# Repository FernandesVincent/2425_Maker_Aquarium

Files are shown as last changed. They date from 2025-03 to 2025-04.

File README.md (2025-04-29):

<header style="
      background-color: #004080;
      color: white;
      padding: 1rem;
      text-align: center;
      height: auto;">
<div class="header-title">
<h1>Aquarium Automatisé</h1>
</div>
</header>

SOMMAIRE
- Préambule
- Objectifs du projet
- Meuble
- Filtration
- Test en gouttes
- Raspberry Pi
- PCB
- Écrans
- Code
- Câblage
- Résultat et Conclusion
- Futur du projet
<h1 style="text-align: center; text-decoration: underline; font-weight: bold;">Préambule</h1>
Aujourd'hui, lorsqu'un particulier achète son aquarium il doit pouvoir gérer un nombre important de facteurs comme la température du bac, la distribution de la nourriture mais également les différents test que peux nécessité son Aquarium (ph, NO2, CO2, etc...). C'est donc dans l'idée de soulager les personnes que cela pèse de devoir s'occuper de tout ça que l'idée du projet d'aquarium automatisé et connecté m'est venue à l'esprit.
<h1 style="text-align: center; text-decoration: underline; font-weight: bold;">Objectifs du Projet</h1>
Pour répondre à la problématique énoncée durant le préambule, j'ai dessiné les différents axes et objectifs du projet énoncés ci-dessous:
- Automatisation des changements d'eau
- Contrôle simple et total sur la luminosité
- Automatisation de la distribution de la nourriture
- Automatisation des test en gouttes
- Contrôle simple de la température
- Afficher le tout sur des écrans
- Bonus : Créer une Application mobile
Afin de réaliser l'ensemble de ces objectifs, j'ai du mettre en oeuvre plusieurs compétences que j'ai pu apprendre durant mon cursus à l'ENSEA telles que:
- Découpe LASER
- Conception de PCBs
- Modélisation et impression 3D
- Sertissage de câbles
- Mécanique
- Soudure
Mais également de nouvelles comme le montage vidéo et le HTML/CSS/JS pour la création d'un site. Pour expliquer chaque partie de ce projet en détail, nous allons partir du plus gros oeuvre vers le plus petit. Commençons donc par parler du meuble qui doit supporter l'aquarium.
<h1 style="text-align: center; text-decoration: underline; font-weight: bold;">Meuble</h1>
Au vu de l'ensemble des objectifs du projet, il fallait un endroit où ranger notamment, l'électronique avec les PCBs et les câbles, le bloc de filtration externe, le dispositif d'analyse des test en gouttes ainsi que les bacs de changements d'eau. Pour répondre à ce besoin j'ai penser à la création d'un meuble pouvant supporter le poids de l'aquarium ainsi que tout ce qu'il y a à l'intérieur. Pour ce faire il a été décidé que la structure du meuble se ferait à l'aide de profilé aluminium 20x40mm et que les murs seront faits en MDF 3mm. Cependant quelques contraintes étaient présentes:
- le meuble doit au minimum faire la largeur (30cm) et la longueur(60cm) de l'aquarium.
- Il doit pouvoir accueillir 2 bacs ayant au minimum une capacité de 18L.
- Le bac doit être assez petit pour diminuer les coûts liés au profilé aluminium.
Prenant tout cela en compte, j'ai réalisés des premiers modèles 3D pour pouvoir estimer la taille du meuble et la quantité de profilé aluminium ainsi que de MDF nécessaire. Vous pouvez voir les modèles prototypes ci-dessous:
<table>
<tbody>
<tr>
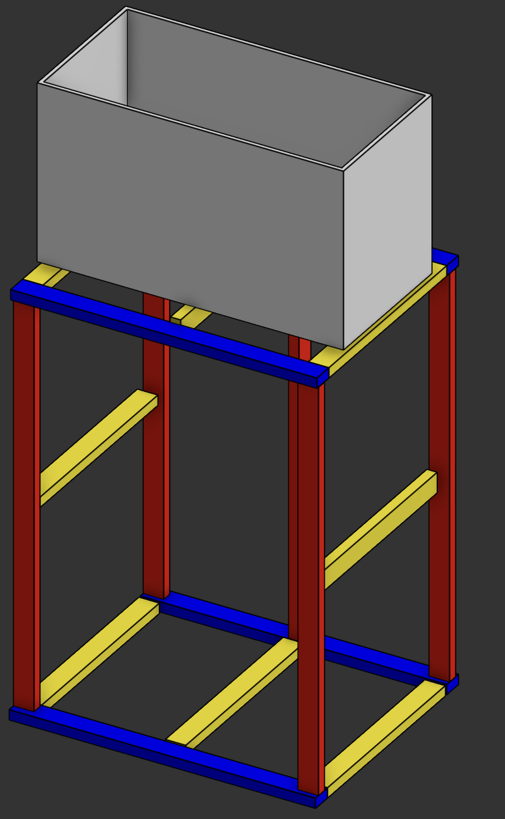
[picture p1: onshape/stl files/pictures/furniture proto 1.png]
<td></td>
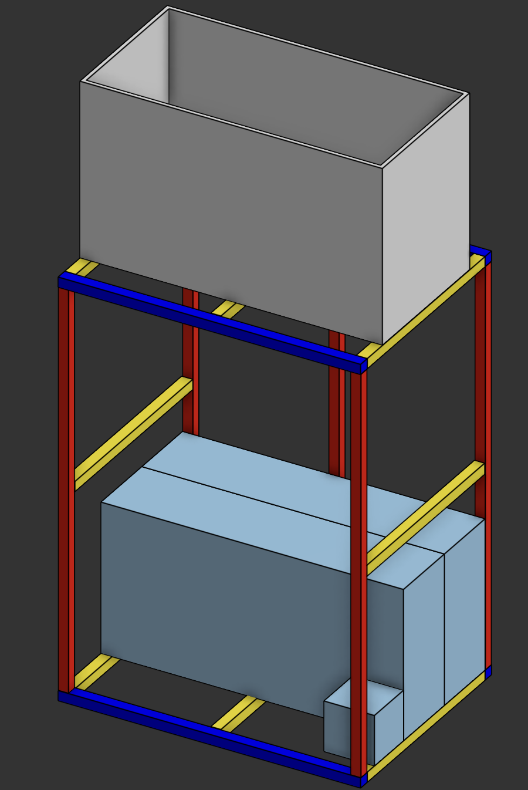
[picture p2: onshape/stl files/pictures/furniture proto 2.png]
<td></td>
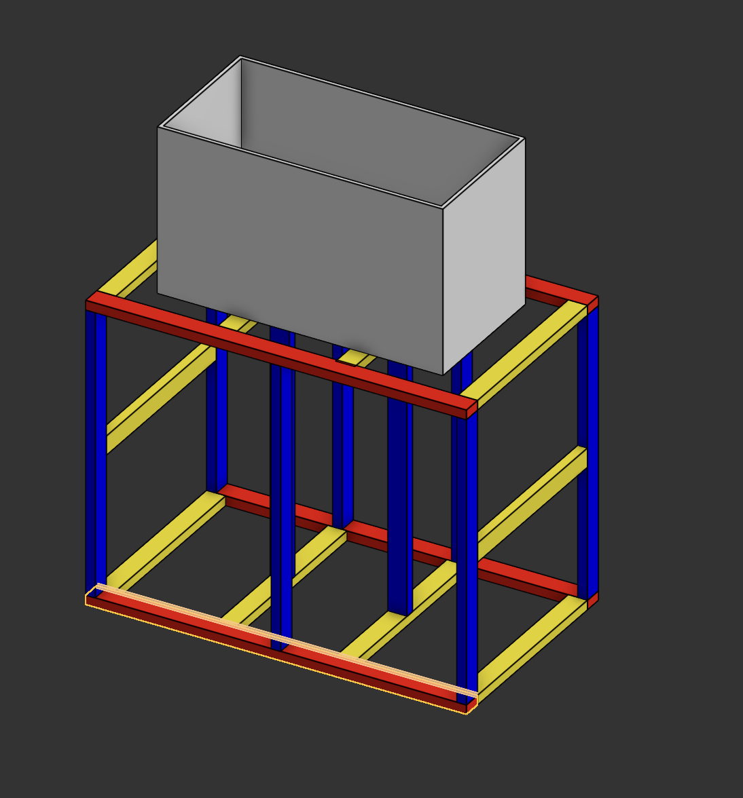
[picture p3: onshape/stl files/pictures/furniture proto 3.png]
<td></td>
</tr>
</tbody>
</table>
<table>
<tbody>
<tr>
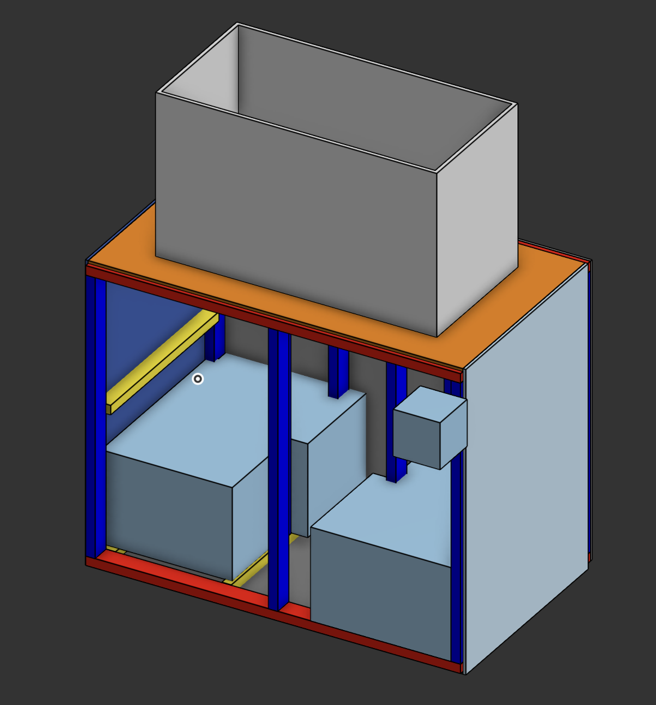
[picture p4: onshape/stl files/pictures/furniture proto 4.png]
<td></td>
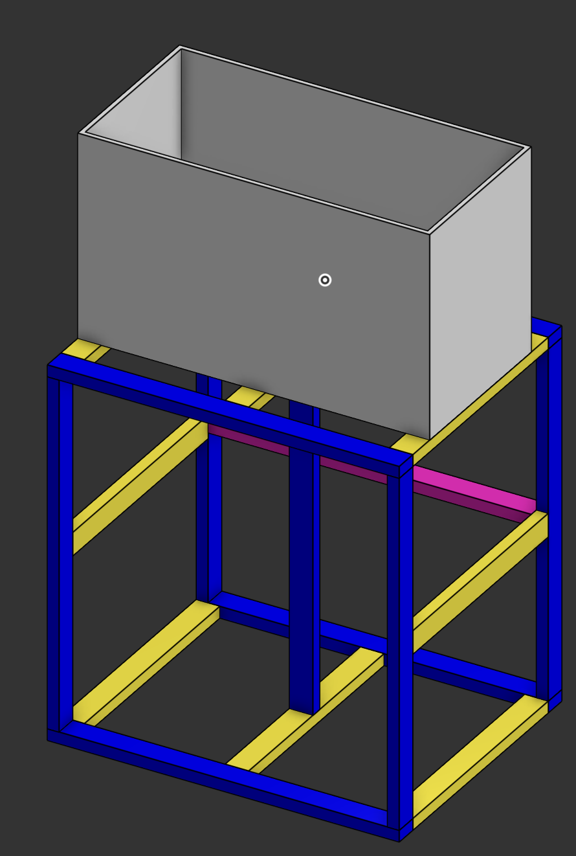
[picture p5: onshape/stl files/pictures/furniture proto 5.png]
<td></td>
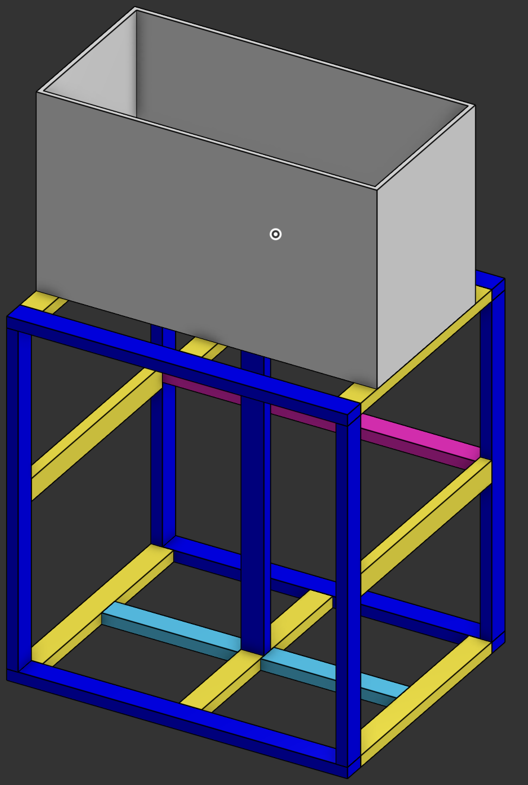
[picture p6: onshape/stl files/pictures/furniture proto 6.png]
<td></td>
</tr>
</tbody>
</table>
La version finale étant la suivante :
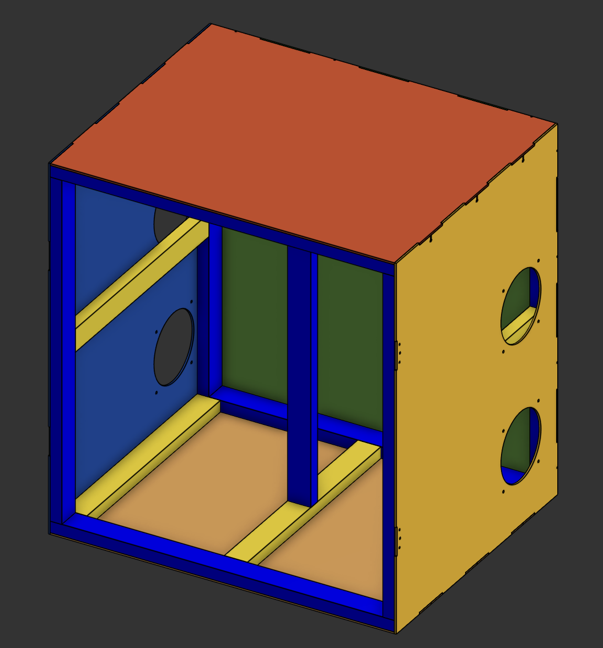
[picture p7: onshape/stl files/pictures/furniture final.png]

L'ensemble des fichiers STL est disponible sur mon
<a href="https://github.com/FernandesVincent/2425_Maker_Aquarium">GitHub</a>
dans la catégorie "onshape".
Ce meuble est donc sur 2 étages, le premier étant un étage réservé aux trois bacs de changements d'eau. Chacun ayant un objectif unique:
<br/>
<br/>
Celui ci-dessous est dédié à l'eau usée de l'aquarium qui peut être réutilisée pour par exemple arroser ses plantes.
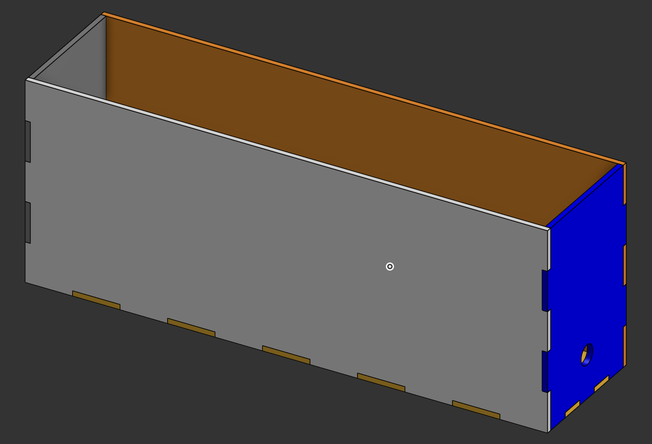
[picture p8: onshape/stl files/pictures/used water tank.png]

Le second présent ci-dessous est fait pour accueillir l'eau propre qui va venir remplacer l'eau usée.
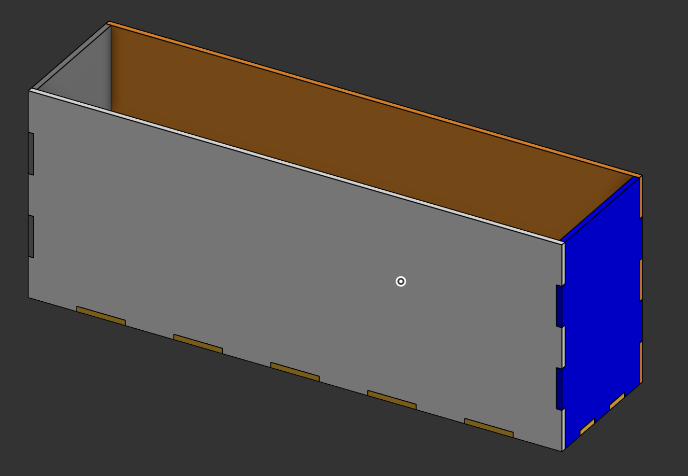
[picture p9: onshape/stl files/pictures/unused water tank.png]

Le troisième et plus petit doit est quant à lui réservé à l'eau en sortie des test à gouttes qui doit être jetée.
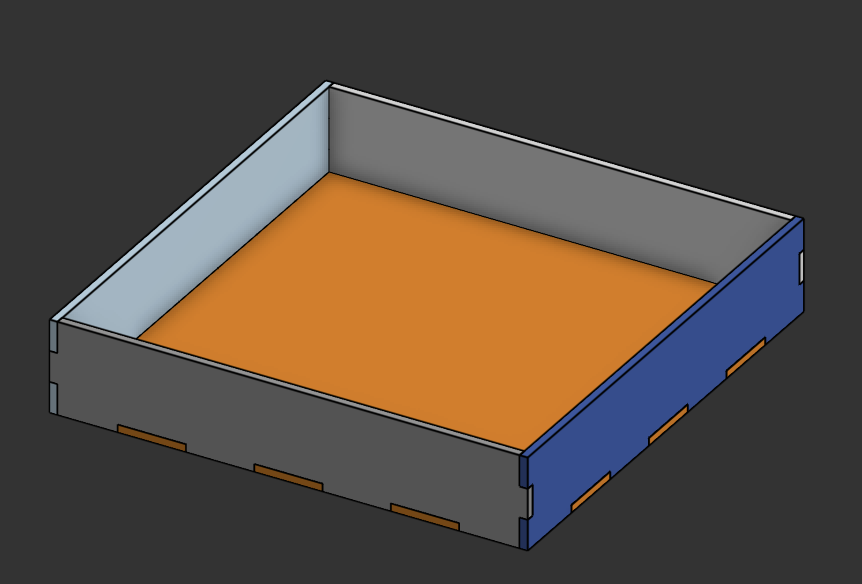
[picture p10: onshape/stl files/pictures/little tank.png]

Pour la sortie du premier bac j'ai trouver un modèle 3D de robinet qui fonctionne assez bien sur
<a href="https://www.printables.com/model/278618-water-tap">Printables</a>
.
De même que précédemment l'ensemble des fichiers STL mais également les fichiers DXF sont disponibles sur mon
<a href="https://github.com/FernandesVincent/2425_Maker_Aquarium">GitHub</a>
dans la catégorie "onshape".
<h1 style="text-align: center; text-decoration: underline; font-weight: bold;">Filtration</h1>
<br/>
Attaquons le second étage du meuble par la partie concernant le bloc de filtration. J'ai souhaité faire ce bloc externe moi-même car cela me permettait de créer un design personnalisé, notamment pour pouvoir y placer aisément le chauffage et la sonde ph en plus des masses filtrantes.
<br/>
Comme précédemment vous pouvez voir ci-dessous le prototype de ce bloc de filtration suivi de la version finale,
<br/>
<br/>
prototype:
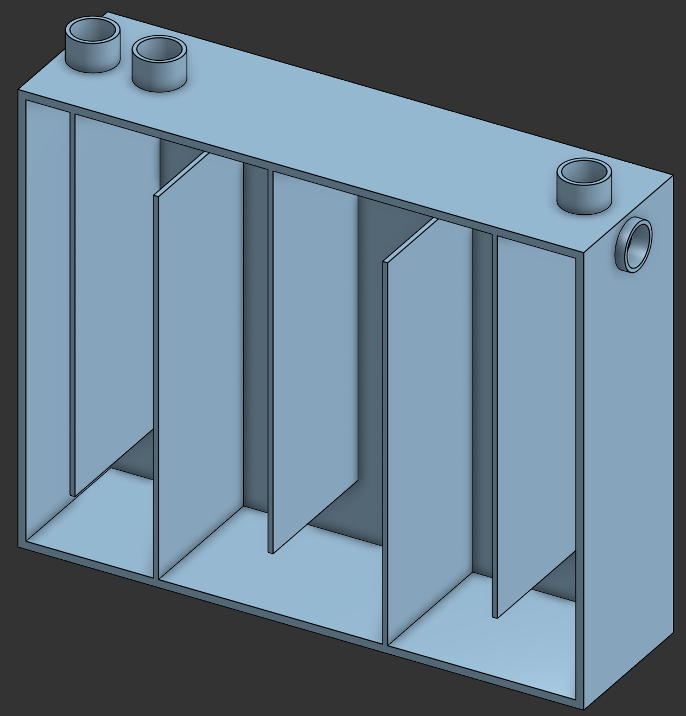
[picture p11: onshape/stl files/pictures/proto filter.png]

<br/>
version finale:
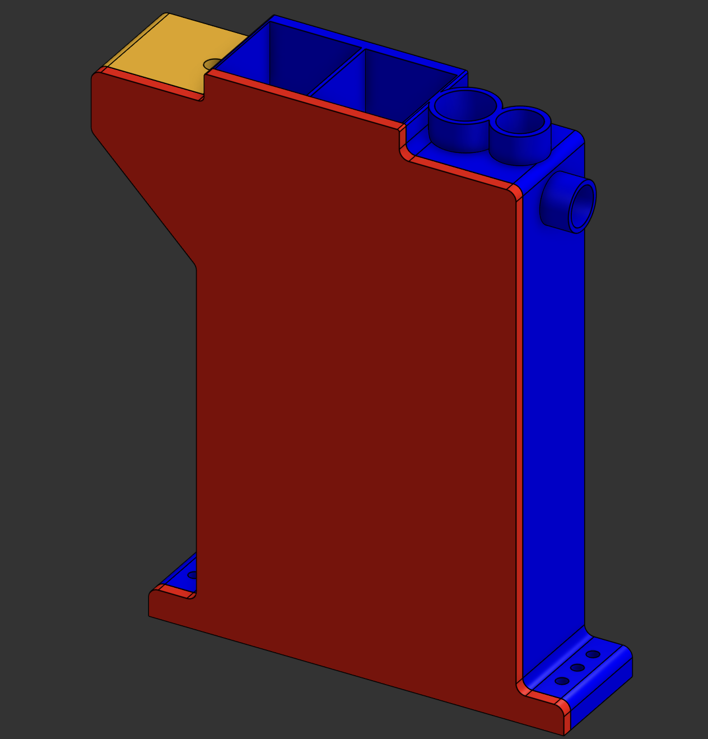
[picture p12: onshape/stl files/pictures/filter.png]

<br/>
<br/>
Pour pouvoir nettoyer les masses filtrantes, j'ai designer un bac de remonté (trouer pour que l'eau s'en écoule et ne pas trempé le meuble en les sortant) avec sa poignée :
<table>
<tbody>
<tr>
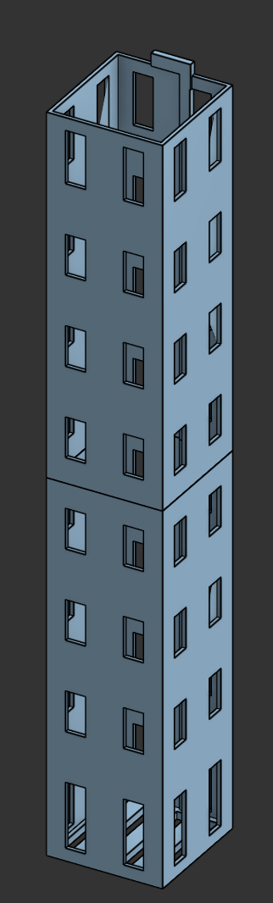
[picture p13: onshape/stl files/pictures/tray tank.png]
<td></td>
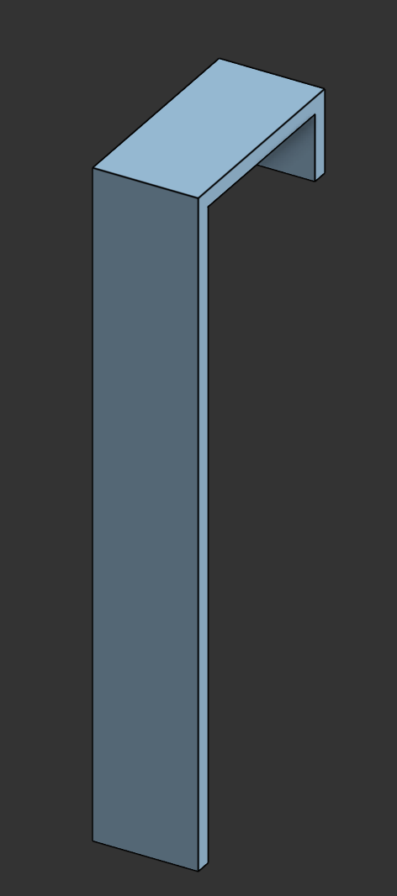
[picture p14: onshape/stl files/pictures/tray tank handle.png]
<td></td>
</tr>
</tbody>
</table>
<br/>
<br/>
Concernant les différents composants de ce bloc, la sonde ph vient de
<a href="https://wiki.dfrobot.com/Gravity__Analog_Spear_Tip_pH_Sensor___Meter_Kit__For_Soil_And_Food_Applications__SKU__SEN0249">DFRobot</a>
tandis que le chauffage est fournis avec l'aquarium qui est un aquarium de 60L de la marque CIANO disponible sur
<a href="https://www.amazon.fr/Aquarium-Poissons-Consommables-Chauffage-Emballage/dp/B0DMZ6JCDD/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">Amazon</a>
.
<br/>
De plus, concernant les masses filtrantes elles sont également disponibles sur Amazon:
<a href="https://www.amazon.fr/Fluval-Pr%C3%A9filtre-pour-Aquariophilie-750/dp/B001CZXZEU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">céramique</a>
;
<a href="https://www.amazon.fr/cyclingcolors-d%C3%A9couper-300x210mm-Universelle-%C3%A9paisseur/dp/B0B8JQTZXK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">mousse</a>
.
<br/>
Les trous dans le Blocs de filtration servent à le fixer dans le plancher à mi hauteur du meuble, ils correspondent à des vis de taille M6 avec une longueur qui doit être d'environ 20 mm sachant que le plancher est fait en MDF 6mm. Des écrous adéquat sont aussi à prévoir.
<br/>
Concernant l'impression du bloc de filtration, elle peut se faire en plus ou moins de parties en fonction de la taille de l'imprimantes. Par exemple, avec les imprimantes disponibles à l'ENSEA :
<br/>
<br/>
Creality K1 Max (300x300x300mm) : 2 parties
<br/>
BambuLab X1 Carbon(250x250x250mm) : 4 parties (les 2 parties précédentes doivent être coupées à mi-hauteur)
<br/>
<br/>
De plus, le bloc a été imprimé en PLA, or le PLA n'est pas étanche. Pour pallier à ce problème j'ai pris l'initiative d'utiliser de la résine époxy afin de vernir le bloc et de le rendre étanche. Le seul inconvénient de cette méthode est la toxicité de la résine notamment durant la phase de catalyse qui peut durer plusieurs heures et nécessite le port d'un
<a href="https://www.amazon.fr/AirGearPro-Protection-Respiratoire-R%C3%A9utilisable-poussi%C3%A8re/dp/B08BQNKK8D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">masque</a>
et de
<a href="https://www.amazon.fr/ARNOMED-jetables-pi%C3%A8ces-nitrile-disponibles/dp/B093SWH4D8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">gants de protection</a>
.
<br/>
<br/>
Pour finir, l'eau arrive du côté de la sonde PH via un tuyaux avec un OD de 20mm et elle ressort de l'autre côté grâce à une pompe de remontée connecter via un raccord à un autre tuyaux.
<br/>
<br/>
<h1 style="text-align: center; text-decoration: underline; font-weight: bold;">Test en gouttes</h1>
Au sein du meuble et à côté du bloc de filtration nous pouvons retrouver la partie test en gouttes du projet. Cette partie est surement la plus complexe du projet car elle implique la modélisation 3D d'un dispositif permettant d'insérer et d'enlever les test en gouttes mais également de pouvoir faire tomber des gouttes lorsque l'on le désire.
<br/>
<br/>
La version actuelle a été réfléchie avec un servomoteur FS90 actionnant un engrenage qui permet à son tour de faire tourner des "bras" qui iront appuyer sur les test afin de faire tomber les gouttes.
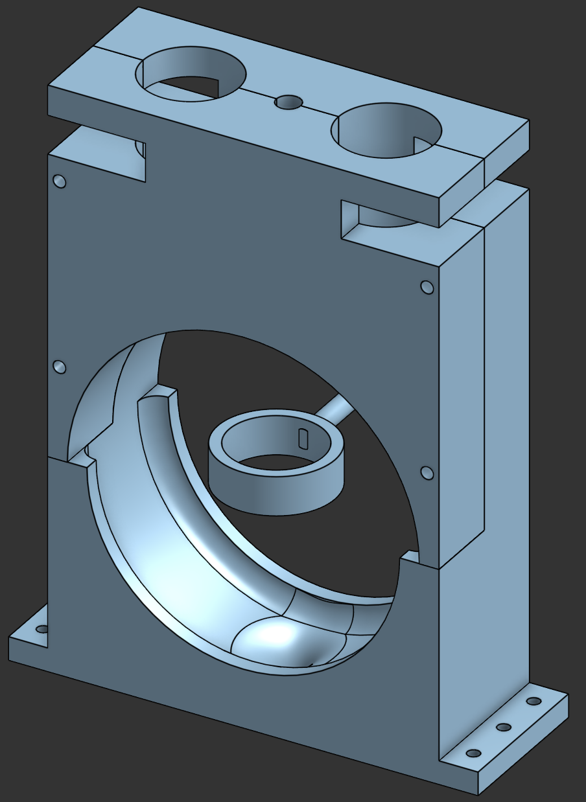
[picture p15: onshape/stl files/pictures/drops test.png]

<br/>
<br/>
Ce mécanisme est malheuresement encore en phase de prototypage car la faible tension de surface au niveau de la sortie goutte à goutte des test implique qu'une seule petite vibration peut faire s'écouler une goutte.
<br/>
Un autre modèle possible serait de faire directement tourner les tests via un servomoteur afin de faire s'écouler la goutte en profitant justement de la faible tension de surface.
<br/>
<br/>
Une fois la goutte écoulée, elle est redirigée dans un flacon, dans lequel s'écoule également l'eau du bac a testée, qui est bloqué par un anneau lié à un autre servomoteur lui permettant de pivoter afin de remuer la solution et enfin de vider le flacon dans un tuyaux menant au bac associé. Afin de déterminer la valeur associé au test (valeur de Ph, de NO3, etc...) il faut effectuer de la reconnaissance colorimétrique.
<h1 style="text-align: center; text-decoration: underline; font-weight: bold;">RaspberryPi</h1>
Pour effectuer la reconnaissance colorimétrique je me suis servi d'un raspberryPi 4 model B avec la module caméra associé. Cet ensemble auquel on ajoute un code en Python, disponible sur mon
<a href="https://github.com/FernandesVincent/2425_Maker_Aquarium">GitHub</a>
dans la catégorie "software", permet de récupérer la vision de la caméra et d'y définir un ou plusieurs points où l'on va vouloir analyser la couleur du pixel en leur centre :
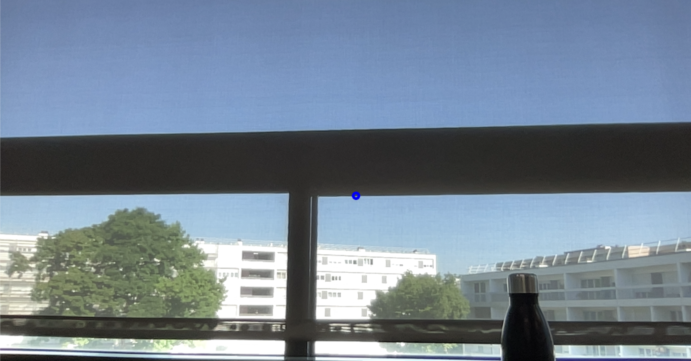
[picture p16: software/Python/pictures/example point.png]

<br/>
Le code couleur que j'ai utilisé est le HSV et non le RGB car cela permet d'être moins sensible à la différence de luminosité.
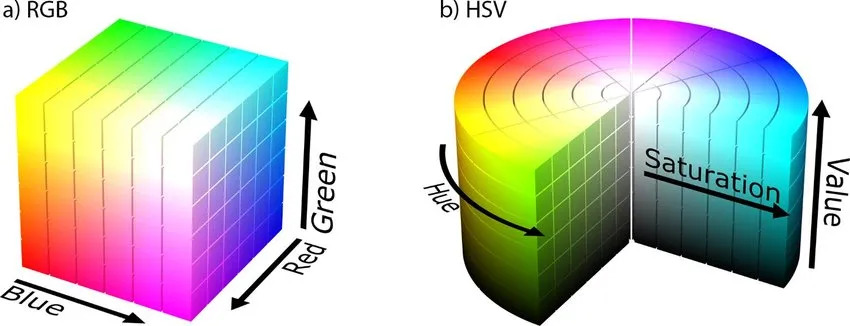
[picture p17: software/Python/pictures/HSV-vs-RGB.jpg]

<br/>
<br/>
Un aspect que je n'ai pas eu le temps de terminer est le fait de comparer les valeurs récupérés par la caméra aux valeurs de références des couleurs des test en gouttes. Cependant, l'idée derrière ce code serait d'avoir pour chaque test un tableau contenant les couleurs références et ainsi via un petit d'algorithme de comparer la couleur HSV expérimental avec celle de référence afin de l'assimiler à celle-ci.
<br/>
Finalement il suffirait de faire correspondre la couleur HSV de référence avec la valeur associée. Une fois cela fait l'objectif est de transmettre cette valeur au PCB principal qui, lui, l'enverra aux écrans.
<h1 style="text-align: center; text-decoration: underline; font-weight: bold;">PCB</h1>
Cela nous fait une transition parfaite pour parler plus en profondeur de la partie PCB du projet. En effet, pour mener à bien ce projet j'ai du réaliser 2 PCB : un premier PCB dit "principal" et un second dit "déporté". Le premier PCB et son aspect de multiprise sert à commander l'ensemble du projet, c'est à dire :
<br/>
<br/>
- Les 4 ventilateurs
- Les 4 pompes
- Les LED
- Les servomoteurs pour le distributeur de nourriture/li>
- Les boutons présents sur le second PCB
- Les écrans
- Les servomoteurs pour les test en gouttes
- la raspberryPi et sa camera
- Les capteurs de niveau d'eau
- Le Ph-mètre
- Le chauffage
- Le ST-Link
- Le HC05
Faisons un petit aparté pour détailler l'utilité de chacun des modules dont nous n'avons pas encore eu l'occasion de discuter.
<br/>
<br/>
<h4>Ventilateurs</h4>
Le meuble et le PCB sont fait pour accueillir 4
<a href="https://www.amazon.fr/ARCTIC-P12-Pack-Refroidisseur-Ventilateur/dp/B07HC7P3HJ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">ventilateurs</a>
12V de 120mmx120mm. Deux (paire entrée/sortie) à l'étage des bacs et deux ( paire entrée/sortie) à l'étage supérieur.
<br/>
Le couple de ventilateur de l'étage inférieur a pour but de ventilé l'eau propre arrivant dans le bac associé afin d'aider à l'évaporation des éléments indésirables contenu dans cette eau (si on utilise de l'eau osmosée ces deux ventilateurs sont inutiles).
<br/>
Le second couple de moteur, quant à lui, est là pour aérer la Pi, le PCB et surtout l'alimentation qui ne possède pas de ventilateur.
<h4>
<br/>
</h4>
<h4>Pompes</h4>
Pour ce projet, nous avons besoins d'un ensemble de 4
<a href="https://www.amazon.fr/submersibles-aquarium-poissons-fontaine-divertissement/dp/B0CDK7GQF2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">pompes</a>
12V 240L/h. Une première sert pour la sortie de la filtration, une seconde à remontée l'eau du bac d'eau propre à l'aquarium, une troisième à vider l'eau de l'aquarium vers le bac de récupération de l'eau usée et la dernière envoi l'eau vers le filtre. Les deux pompes liées à la filtrations fonctionnent en continu tandis que les deux autres fonctionne sur commande grâce à l'utilisation de deux transistors NMOS présents sur le PCB permettant d'allumer les pompes quand le GPIO lié à leur Ground est à l'état haut.
<h4>
<br/>
</h4>
<h4>LED</h4>
Les LED de ce projet sont séparées en deux parties mais viennent toutes de la même bande
<a href="https://www.amazon.fr/Jun-Saxifragelec-lumineuse-flexible-adressable-individuellement/dp/B0B8N4V9HW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">Neopixel</a>
.
<h4>
<br/>
</h4>
<h5>LED internes</h5>
Ce sont des LEDs coupées du ruban et placées dans le meuble afin de pouvoir l'éclairer en continu avec une même luminosité afin de limiter au mieux les erreurs de reconnaissances colorimétriques.
<h4>
<br/>
</h4>
<h5>LED externes</h5>
Ces LED sont le reste du ruban et servent directement à l'éclairage de l'aquarium. L'utilité d'avoir pris des LED Neopxiel est ici de pouvoir totalement configurer la couleur que l'on veut pour éclairer son aquarium en fonction des poissons et plantes qui l'occupe.
<h4>
<br/>
</h4>
<h4>Servomoteurs (nourriture)</h4>
Je vais traiter directement ici la partie de la distribution automatique de la nourriture car je n'ai pas eu le temps de la réaliser et par conséquent elle ne nécessite pas une partie entière à elle seule. L'objectif de cette partie était initialement de pouvoir automatiser la distribution de nourriture via un système de courroie de transmission qui amène la nourriture depuis une entrée (image ci-dessous) jusqu'à une trappe qui s'ouvre ou se ferme via l'utilisation d'un servomoteur, le tout installé à l'intérieur de la ramp LED qui éclaire l'aquarium.
<br/>
<br/>
<br/>
Ce dispositif, au même titre que les bacs de changement d'eau, permettrait à l'usager de pouvoir partir en vacances ou autre tout en sachant que les poissons seront nourris et que les changements d'eau se feront. Le problème majeur qui a fait que je n'ai pas pu réaliser cette partie est la création de la courroie de transmission qui doit être assez petite pour pouvoir faire en sorte que la rampe LED ne devienne pas trop massive autant d'un point de vu visuel que du point de vu de sa masse.
<h4>
<br/>
</h4>
<h4>Boutons</h4>
Les boutons sont placés sur le PCB secondaire et sont au nombre de 6, 3 paires de 2 boutons. Chaque paire permet d'ajuster un paramètre, la première paire permet d'ajuster la température, la deuxième la température et la troisième la fréquence de la distribution de nourriture.
<h4>
<br/>
</h4>
<h4>Écrans</h4>
Le PCB secondaire est également connecté à 6
<a href="https://www.gotronic.fr/art-afficheur-oled-0-96-128-x-64-grove-33932.htm">écrans</a>
OLED dont l'objectif est d'afficher les différents paramètres de notre système, que ce soit la température, la luminosité ou bien els différents test de l'eau.
<h4>
<br/>
</h4>
<h4>Capteurs de niveau d'eau</h4>
Ces
<a href="https://www.adafruit.com/product/4965">capteurs</a>
servent, comme leur nom l'indique, à vérifier le niveau de l'eau. Je me suis procuré ceux de Adafruit car leur prix est peu élevé et qu'ils suffisent pour l'utilité que j'en ai.
<br/>
<br/>
Lorsque deux bandes de métal entrent en contact avec de l'eau cela crée un court-circuit ce qui renvoie un signal au PCB (état haut : il ya la présence de court circuit donc l'eau à atteint le niveau que l'on veut vérifier tandis qu'à l'état bas ce n'est pas le cas). J'ai prévu d'en placer un dans l'aquarium, un autre dans le bac d'eau usée et un dernier dans le bac d'eau propre. Tout les trois servant à indiquer que l'on a atteint une hauteur limite au dessus de laquelle il se peut que l'eau se déserve des bacs.
<h4>
<br/>
</h4>
<h4>Ph-mètre</h4>
Ce Ph-mètre est fournis avec la sonde Ph et permet de rendre lisible la tension que sort la sonde Ph. Dans le futur du projet il me plairait de réussir à en faire un moi même.
<h4>
<br/>
</h4>
<h4>Chauffage</h4>
Fournis avec l'aquarium, l'objectif serait d'y connecter un servomoteur afin de pouvoir sélectionner la température que l'on souhaite avec le module externe où se trouve le PCB déporté ainsi que les écrans.
<h4>
<br/>
</h4>
<h4>ST-Link</h4>
Simplement présent pour pouvoir programmer le microprocesseur.
<h4>
<br/>
</h4>
<h4>HC05</h4>
J'ai prévu un connecteur pour le module HC05 même si l'utilisation de celui-ci ne se fera qu'à la toute fin du projet. L'objectif étant de connecter un pc ou un téléphone en bluetooth à ce module afin de récupérer l'ensemble des paramètres comme le font les écrans mais cette fois sur un pc ou un téléphone, l'objectif ultime étant le développement d'une appilcation.
<br/>
<br/>
<br/>
<br/>
<br/>
Revenons en aux PCBs, vous l'aurez compris mais ici nous avons 2 PCB avec des rôles bien distinct, le premier servant à contrôler l'ensemble du projet tandis que le second ne gère que les boutons et à se connecter aux écrans. Vous pouvez trouver ci-dessous deux photos par PCB suivies d'un lien, les photos correspondent aux schemtatic et routage des PCB effectués sous KiCad 9.0 et le fichier quant à lui est la Bill Of Material (BOM) contenant l'ensemble des composants nécessaires à la fabrication des PCB.
<br/>
<br/>
PCB principal:
<table>
<tbody>
<tr>
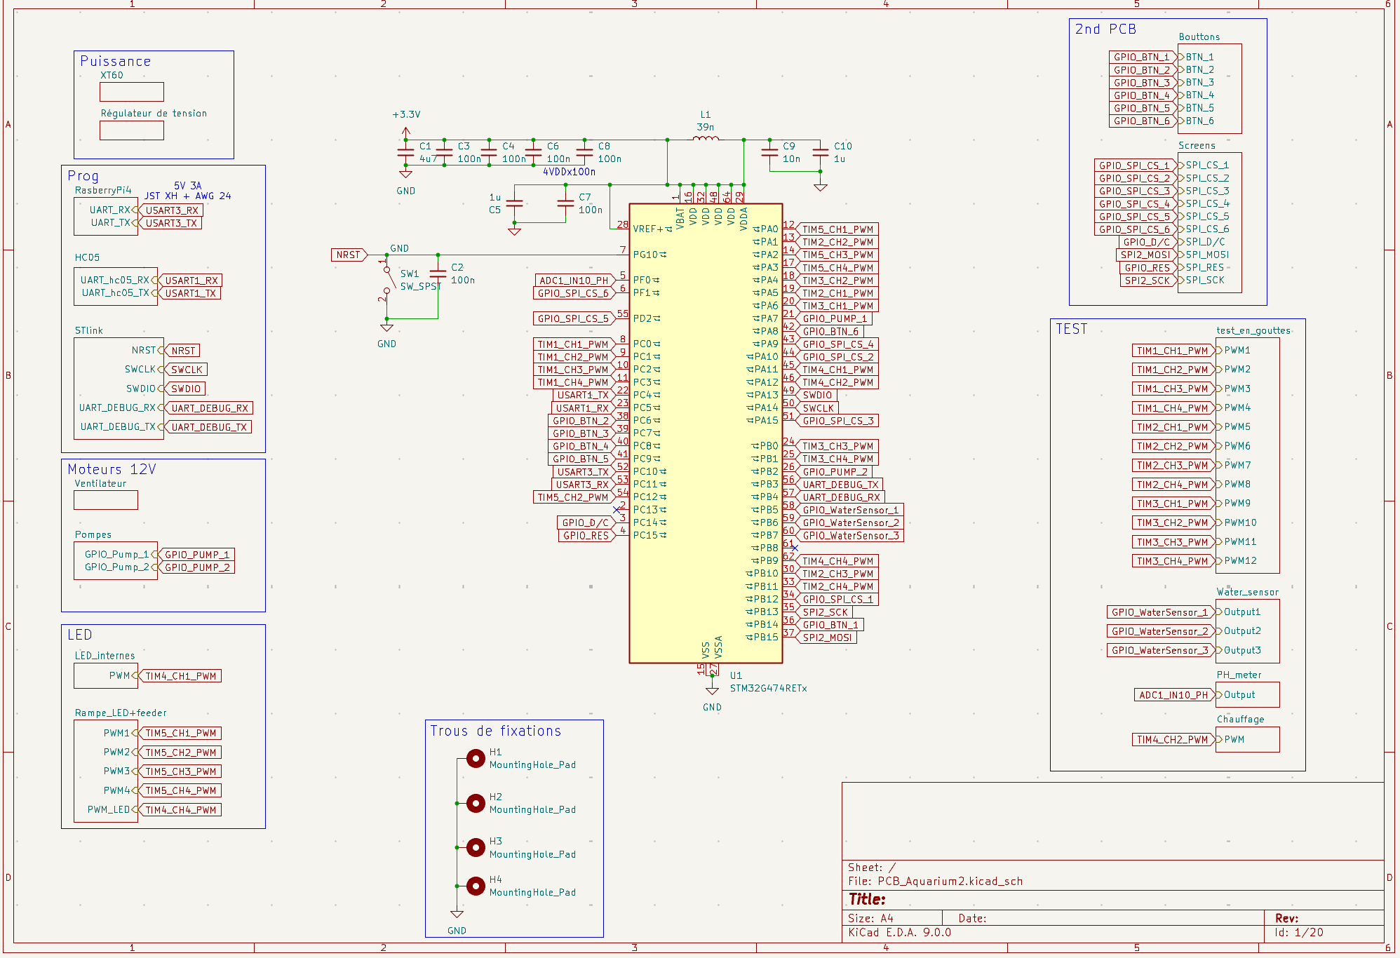
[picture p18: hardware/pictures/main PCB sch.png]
<td></td>
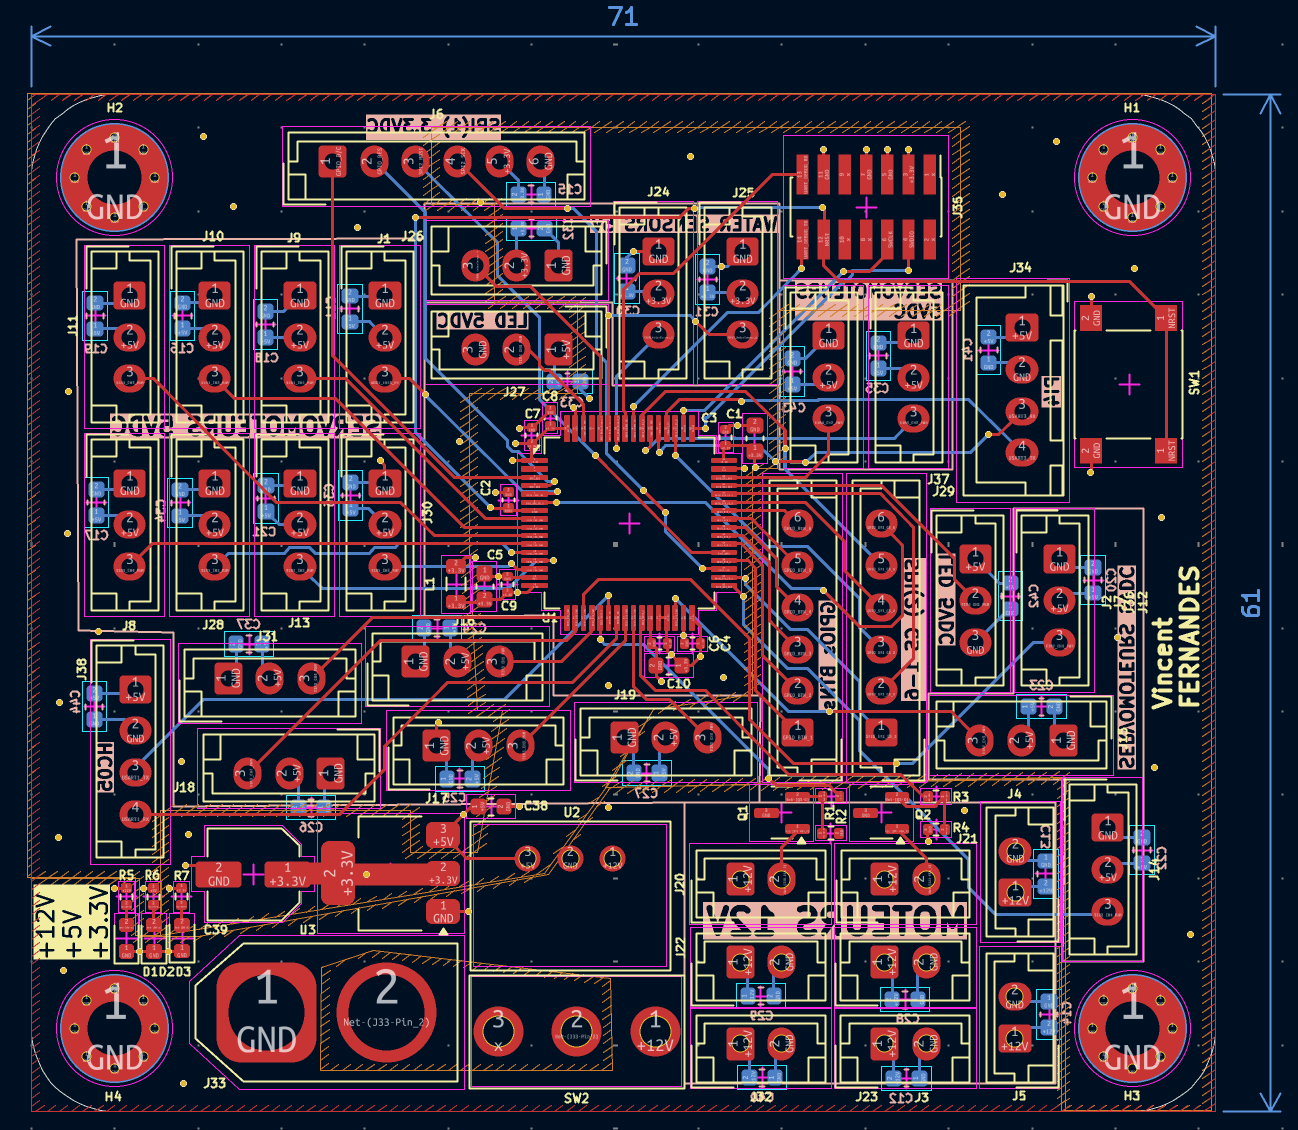
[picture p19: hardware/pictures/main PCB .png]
<td></td>
</tr>
</tbody>
</table>
<a href="https://github.com/FernandesVincent/2425_Maker_Aquarium/blob/main/hardware/PCB_Aquarium2/BOM_PDF.pdf">BOM</a>
<br/>
<br/>
PCB secondaire:
<table>
<tbody>
<tr>
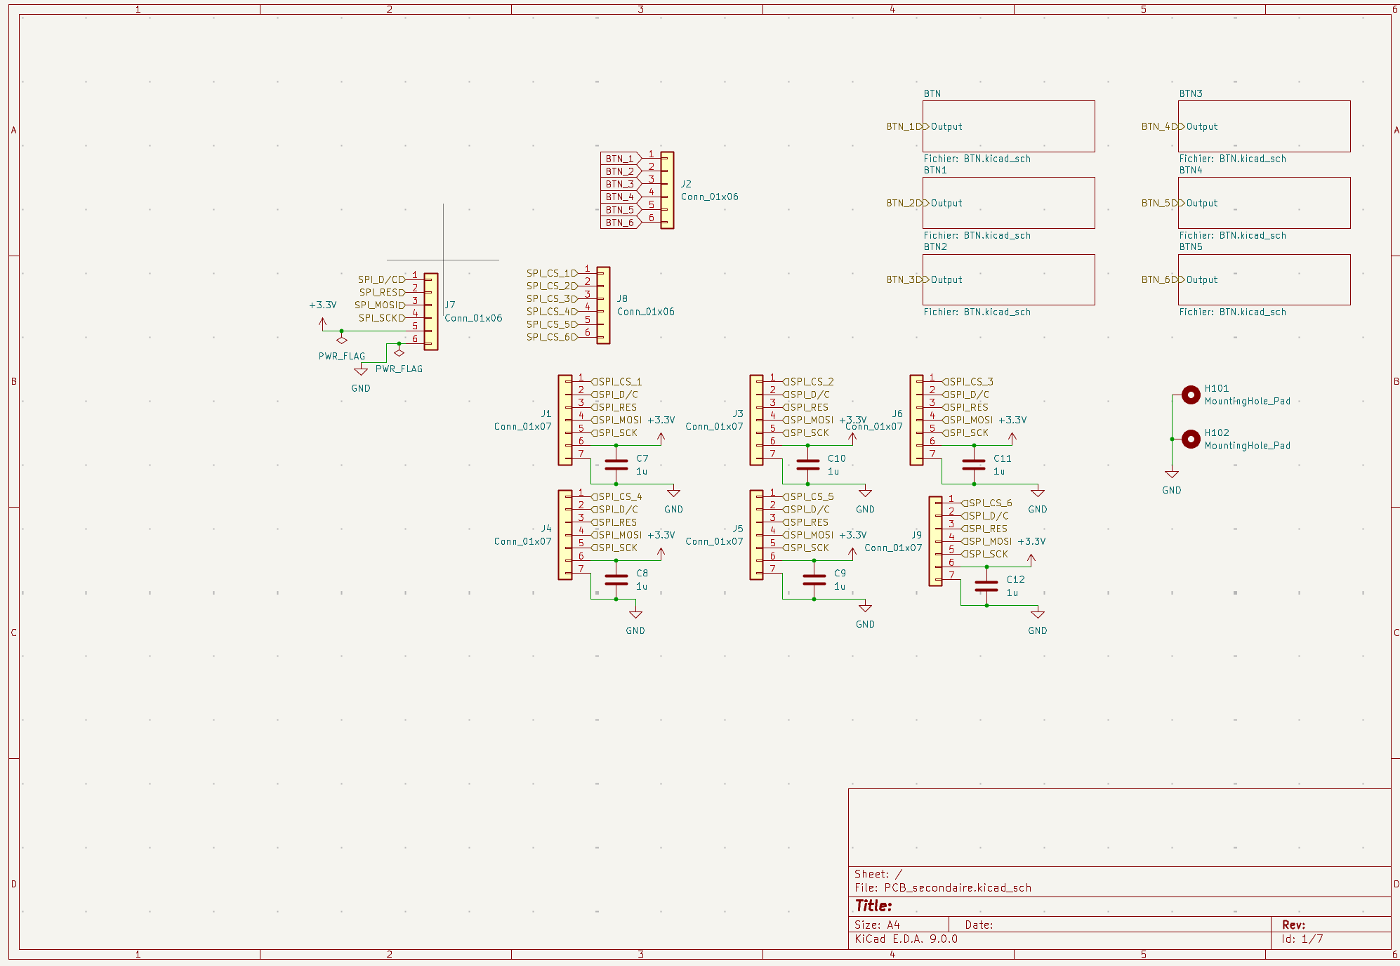
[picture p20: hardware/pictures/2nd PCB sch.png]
<td></td>
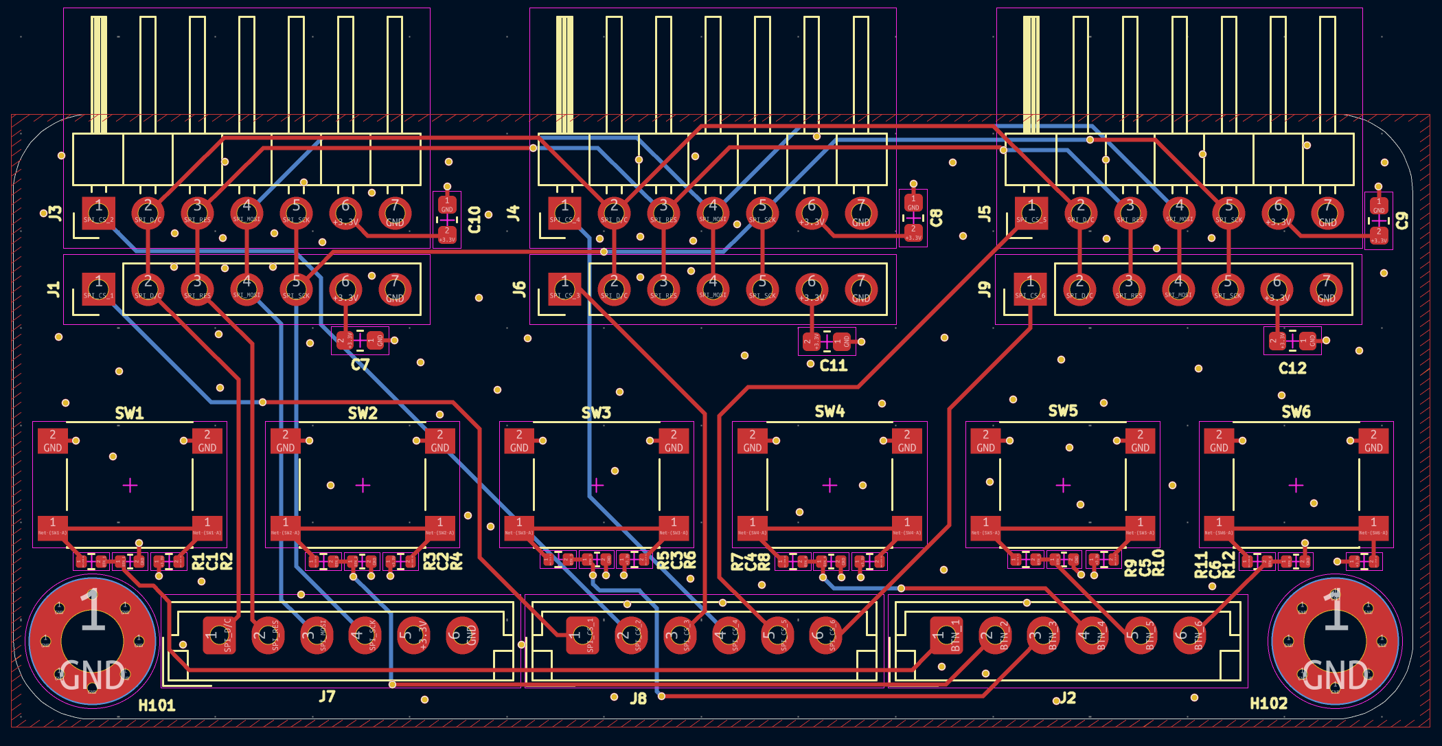
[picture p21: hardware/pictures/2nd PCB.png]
<td></td>
</tr>
</tbody>
</table>
<a href="https://github.com/FernandesVincent/2425_Maker_Aquarium/blob/main/hardware/PCB_secondaire/BOM_PDF.pdf">BOM</a>
<h1 style="text-align: center; text-decoration: underline; font-weight: bold;">Écrans</h1>
Nous avons d'ores et déjà parlé succinctement du rôle des écrans dans le projet c'est pourquoi j'aimerais m'attarder ici plutôt sur la partie code associé à ces écrans. En effet, Les écrans que j'ai commandé sont les suivants:
<br/>
<br/>
Ces écrans peuvent communiquer soit en I2C (avec 2 adresses possibles : 0x7A et 0x78) soit en SPI. Or, et je pense que vous l'avez compris avec la partie précédente mais nous avons beaucoup de modules différents avec lesquels le microprocesseur doit communiquer. Le microprocesseur en question est le STM32G474RET6 qui possède 3 I2C, ce qui est parfait pour notre projet car nous pouvons commander 2 écrans avec un seul I2C. Mais à cause du nombre très élevés du nombre de pins que le microprocesseur doit allouer au reste du projet, les pins que les 3 I2C utilisent ne sont plus disponibles.
<br/>
Il m'a donc fallu me rabattre sur le SPI qui bien que nécessitant un nombre de pins plus élevés est plus pratique dans ce cas pour deux : 1 seul SPI peut gérer les 6 écrans à conditionner de leur réservé un pin de sélection (Chip Select (CS)) chacun mais également car la plupart des pins qu'il utilise peuvent être de simple GPIO (comme CS) voir même non obligatoire en fonction de l'utilisation.
<br/>
Par exemple dans notre cas nous n'avons pas besoin du pin MOSI (Master Out Slave In) car on attend pas de réponse de la part des écrans.
<br/>
Le problème majeur que j'avais concernant le SPI est que je n'avais jamais travaillé ce protocole auparavant, j'ai donc du apprendre comment il fonctionne ce qui ne fut, heureusement, pas la partie la plus compliquée. Cependant, là où je me suis heurté à un mur c'est au moment de la recherche de librairies pour utiliser ce protocole avec le driver de mes écrans (le SSD1315) qui n'est malheureusement pas le driver le plus utilisé ce qui implique donc que les librairies que j'ai trouvées n'avaient pas directement de librairies pour ce driver, même si il semblerait que celles du driver SSD1306 fonctionne, du moins en partie, avec le SSD1315. De plus, j'ai également reçu de la part de mon encadrant une library faîte pour mon driver mais en I2C.
<br/>
Au vu du temps qu'il me restait à ce moment là j'ai préféré me concentrer sur d'autres aspects du projet ce qui fait qu'à l'heure où j'écris ces lignes, les écrans ne sont pas encore fonctionnels.
<h1 style="text-align: center; text-decoration: underline; font-weight: bold;">Code</h1>
Nous avons déjà eu l'occasion d'aborder le sujet du code dans ce projet mais j'aimerais y dédier une partie car il y a quand même des notions à ajouter et que je ne pourrais diluées dans aucune aitre partie. Veuillez tout d'abord regarder le diagramme d'architecture du code présent ci-dessous:
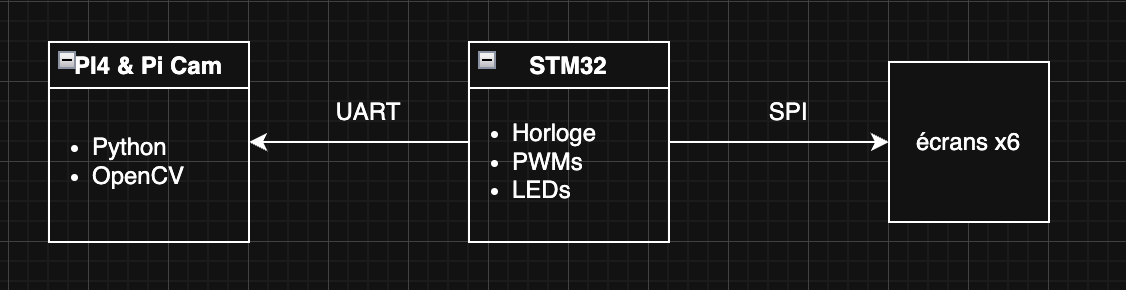
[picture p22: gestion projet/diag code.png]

<br/>
Nous avons déjà aborder la partie de la RaspberryPi excepté le fait que pour effectué la reconnaissance colorimétrique j'ai du utiliser OpenCV.
<br/>
<br/>
Concernant le code du STM32 il est, je pense, nécessaire de recontextualiser: Pour ce projet nous devons effectué des changements d'eau à un intervalle fixe (10% de l'eau de l'aquarium chaque semaine), de même il faut nourrir les poissons et effectuer les test en gouttes à intervalles réguliers. Pour effectuer cela sachant que le projet n'est pas connecté à Internet, il m'a fallu créer un horloge interne qui peux fonctionner d'elle même après avoir flasher le microprocesseur avec le code présent sur mon PC. Le fichier la contenant peut être trouver sur mon GitHub. Cette Horloge démarre à partir d'un date définit arbitrairement et permet de réaliser des actions du type : si on est au jour X à l'heure Y et à la minute Z : fait telle action.
<br/>
De plus, comme je ne commande en moteur que des servomoteurs basiques, il me suffit de leur envoyer des PWMs pour définir la position d'arrivé et ensuite les faire revenir à leur positions de départ une fois leur action finie. Le seul inconvénient de cela est que dois tester chaque mouvement de mes servomoteurs pour plusieurs valeurs de PWMs afin de pouvoir savoir quelle valeur de PWM serait la meilleure. Une méthode plus évoluée serait de créer une boucle for qui incrémente la valeur de la PWM à chaque itération.
<br/>
Finalement, Les LEDs sont commandées via DMA grâce à une librairie crée par l'un des professeurs de l'école. La seule chose est que je dois définir des valeurs références pour la couleur des LEDs afin que l'usager puisse par l'appui des boutons, passer d'une couleur à une autre. Une amélioration serait d'avoir 3 encodeur rotatif permettant à l'usager d'avoir la possibilité de régler la couleur de la lumière de son précision avec une précision qu'il n'a pas actuellement.
<h1 style="text-align: center; text-decoration: underline; font-weight: bold;">Câblage</h1>
Au vu du projet et du nombre de modules à connecter aux PCB vous vous doutez que le nombre de câbles à sertir est conséquent ! Et c'est effectivement le cas.
<br/>
Pour ce projet j'ai du sertir énormément de câbles pour différents types de connecteurs : JST EH, JST XH, Duponts. De plus, j'ai également du simplement dénuder des câbles afin de pouvoir les souder à d'autres notamment pour les pompes ou les câbles d'alimentation.
<br/>
Mais le câblage ne s'arrête pas à sertir un câble, il faut également les emballer. C'est à dire qu'il faut entourer les câble de gaine tressée pour les protéger mécaniquement et thermiquement mais également pour les organiser. Mais il faut également les entourer de gaine thermorétractable pour fixer la gaine tressée aux câbles au niveau des extrémités pour pas qu'elle ne bouge mais également au niveau des points de soudure pour protéger ce point notamment si il y a un autre câble souder à côté, ils sont ainsi isolés l'un de l'autre et l'on ne risque pas de mauvais contacts.
<h1 style="text-align: center; text-decoration: underline; font-weight: bold;">Résultat Final et Conclusion</h1>
Tout au long de cette présentation vous avez pu voir différentes parties du projet mais il est temps de montrer le résultat que j'ai réussi à obtenir à la fin de ce proje ainsi que la vidéo de présentation du projett:
<br/>
<a href="https://github.com/FernandesVincent/2425_Maker_Aquarium/blob/main/gestion%20projet/final%20result.mp4">
<br/>Résultat final</a>
<br/>
<a href="https://github.com/FernandesVincent/2425_Maker_Aquarium/blob/main/gestion%20projet/Vid%C3%A9o%20Aquarium.mp4">vidéo de présentation</a>
<br/>
<br/>
Comme vous pouvez le voir je n'ai pas pris de vidéos avec l'aquarium remplit et le système en fonctionnement et la raison à cela est simple: je n'ai pas réussi à finir et emboiter toutes les parties du projet dans le temps impartit.
<br/>
<br/>
Pour conclure cette présentation j'aimerais revenir sur ce qu'à pu m'apporter ce projet. En effet, ce projet malgré le fait que je n'ai pas pu le finir m'a quand même permis de développer toutes les compétences que l'on a pu développées au cours de cette présentation, des compétences que j'avais déjà mais que j'ai pu grandement améliorées comme la création et la soudure de PCB ou bien des compétences que je n'avais pas encore eu l'occasion de développer durant mon parcours comme la découpe LASER, la modélisation et l'impression 3D.
<br/>
Au vu de mon niveau, ce projet était sans nul doute ambitieux, surement trop d'ailleurs au vu du temps impartit mais c'est ce qui en fait un bon projet dans le sens où j'ai pu apprendre comme je n'ai jamais appris avec n'importe quel autre projet.
<h1 style="text-align: center; text-decoration: underline; font-weight: bold;">Futur du Projet</h1>
Bien évidemment je ne compte pas m'arrêter là pour ce projet. En effet, il me reste un an pour le finir avant de finir mes études et je compte bien profiter de cette année pour finir le projet et y apporter toutes les améliorations dont j'ai pu parler au sein de cette présentation et qui sait peut-être que d'autres me viendront à l'esprit entre temps !

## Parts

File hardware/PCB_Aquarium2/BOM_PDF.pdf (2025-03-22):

### BOM

Reference | Qty | Value | Footprint | MPN
C1 | 1 | 4u7 | Capacitor_SMD:C_0603_1608Metric
C2,C3,C4,C6,C7,C8 | 6 | 100n | Capacitor_SMD:C_0402_1005Metric
C5,C10,C11,C12,C13,C14,C15,C16,C17,C18,C19,C20,C21,C22,C23,C24,C25,C26,C27,C28,C29,C30,C31,C32,C33,C34,C35,C36,C37,C40,C41,C42,C43,C44 | 34 | 1u | Capacitor_SMD:C_0603_1608Metric
C9 | 1 | 10n | Capacitor_SMD:C_0402_1005Metric
C38 | 1 | 10u | Capacitor_SMD:C_0603_1608Metric
C39 | 1 | 22u | Capacitor_SMD:C_Elec_5x5.4
D1,D2,D3 | 3 | RED_LED | LED_SMD:LED_0603_1608Metric | 150060RS55040
H1,H2,H3,H4 | 4 | MountingHole_Pad | MountingHole:MountingHole_3.2mm_M3_Pad_Via
J1,J8,J9,J10,J11,J12,J13,J14,J15,J16,J17,J18,J19,J24,J25,J26,J27,J28,J29,J30,J31,J36,J37 | 23 | Conn_01x03 | Connector_JST:JST_EH_B3B-EH-A_1x03_P2.50mm_Vertical
J2,J6,J7 | 3 | Conn_01x06 | Connector_JST:JST_EH_B6B-EH-A_1x06_P2.50mm_Vertical
J3,J4,J5,J20,J21,J22,J23,J32 | 8 | Conn_01x02 | Connector_JST:JST_EH_B2B-EH-A_1x02_P2.50mm_Vertical
J33 | 1 | Conn_01x02 | Connector_AMASS:AMASS_XT60-M_1x02_P7.20mm_Vertical
J34 | 1 | Conn_01x04 | Connector_JST:JST_XH_B4B-XH-A_1x04_P2.50mm_Vertical
J35 | 1 | Conn_ST_STDC14 | Connector_PinHeader_1.27mm:PinHeader_2x07_P1.27mm_Vertical_SMD | STLINK-V3MINIE
J38 | 1 | Conn_01x04 | Connector_JST:JST_EH_B4B-EH-A_1x04_P2.50mm_Vertical
L1 | 1 | 39n | Inductor_SMD:L_0805_2012Metric
Q1,Q2 | 2 | NMOS | Package_TO_SOT_SMD:SOT-23 | SQ2310ES
R1,R3 | 2 | 1k | Resistor_SMD:R_0402_1005Metric
R2,R4 | 2 | 10k | Resistor_SMD:R_0402_1005Metric
R5 | 1 | 5k1 | Resistor_SMD:R_0402_1005Metric
R6 | 1 | 1k6 | Resistor_SMD:R_0402_1005Metric
R7 | 1 | 820 | Resistor_SMD:R_0402_1005Metric
SW1 | 1 | SW_SPST | mylib:SW_Push_1P1T_NO_6x6mm_H9.5mm
SW2 | 1 | SW_SPDT | mylib:472123010111 | 472123010111
U1 | 1 | STM32G474RETx | Package_QFP:LQFP-64_10x10mm_P0.5mm
U2 | 1 | 173010578 | Library:173010542 | 173010578
U3 | 1 | AZ1117-3.3 | Package_TO_SOT_SMD:SOT-223-3_TabPin2 | AZ1117CH2-3.3TRG1

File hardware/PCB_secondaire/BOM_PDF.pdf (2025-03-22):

### BOM_CSV

Reference | Qty | Value | Footprint
C1,C2,C3,C4,C5,C6 | 6 | 10n | Capacitor_SMD:C_0402_1005Metric
C7,C8,C9,C10,C11,C12 | 6 | 1u | Capacitor_SMD:C_0603_1608Metric
H101,H102 | 2 | MountingHole_Pad | MountingHole:MountingHole_3.2mm_M3_Pad_Via
J1,J6,J9 | 3 | Conn_01x07 | Connector_PinHeader_2.54mm:PinHeader_1x07_P2.54mm_Vertical
J2,J7,J8 | 3 | Conn_01x06 | Connector_JST:JST_EH_B6B-EH-A_1x06_P2.50mm_Vertical
J3,J4,J5 | 3 | Conn_01x07 | Connector_PinHeader_2.54mm:PinHeader_1x07_P2.54mm_Horizontal
R1,R2,R3,R4,R5,R6,R7,R8,R9,R10,R11,R12 | 12 | 10k | Resistor_SMD:R_0402_1005Metric
SW1,SW2,SW3,SW4,SW5,SW6 | 6 | SW_SPST | mylib:SW_Push_1P1T_NO_6x6mm_H9.5mm

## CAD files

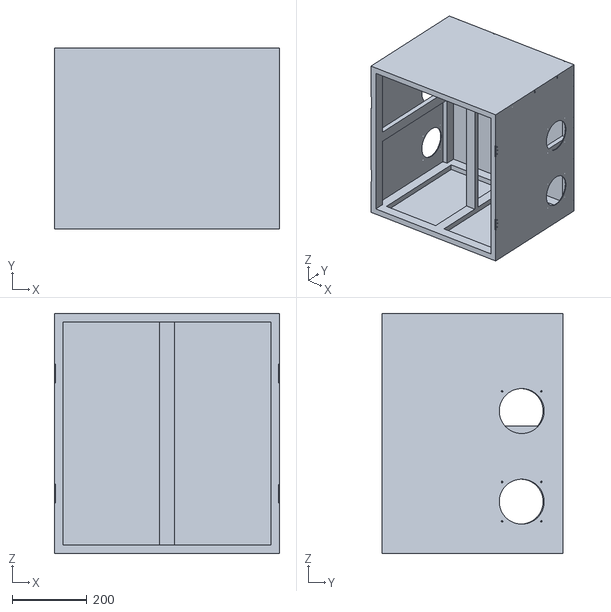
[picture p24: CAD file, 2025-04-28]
onshape/stl files/furniture assembly.stl
601.0 x 483.0 x 641.0

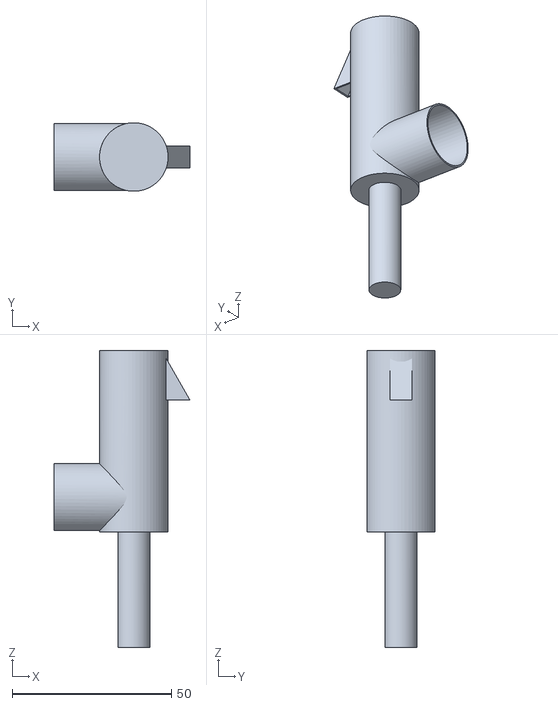
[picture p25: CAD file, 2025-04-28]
onshape/stl files/prototypes/pump assembly.stl
42.6 x 21.5 x 93.2

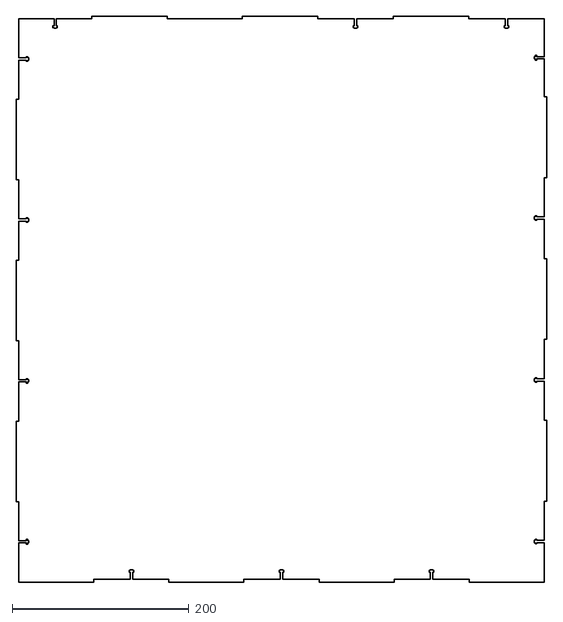
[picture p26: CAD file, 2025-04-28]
onshape/dxf files/back.dxf
601.0 x 641.0

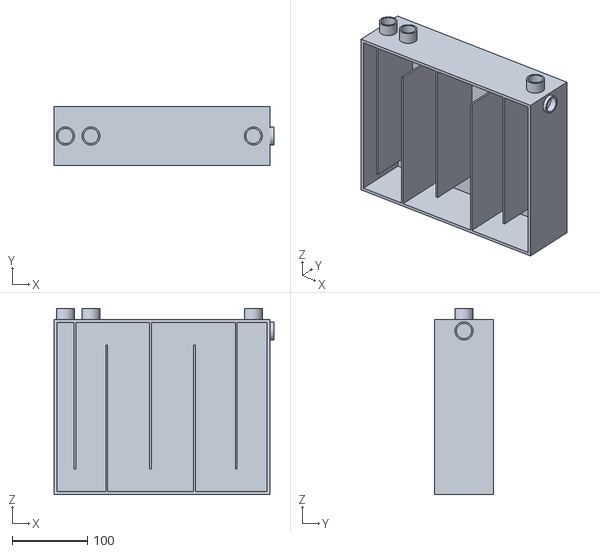
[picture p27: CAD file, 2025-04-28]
onshape/stl files/prototypes/proto filter v1.stl
293.0 x 79.0 x 248.0

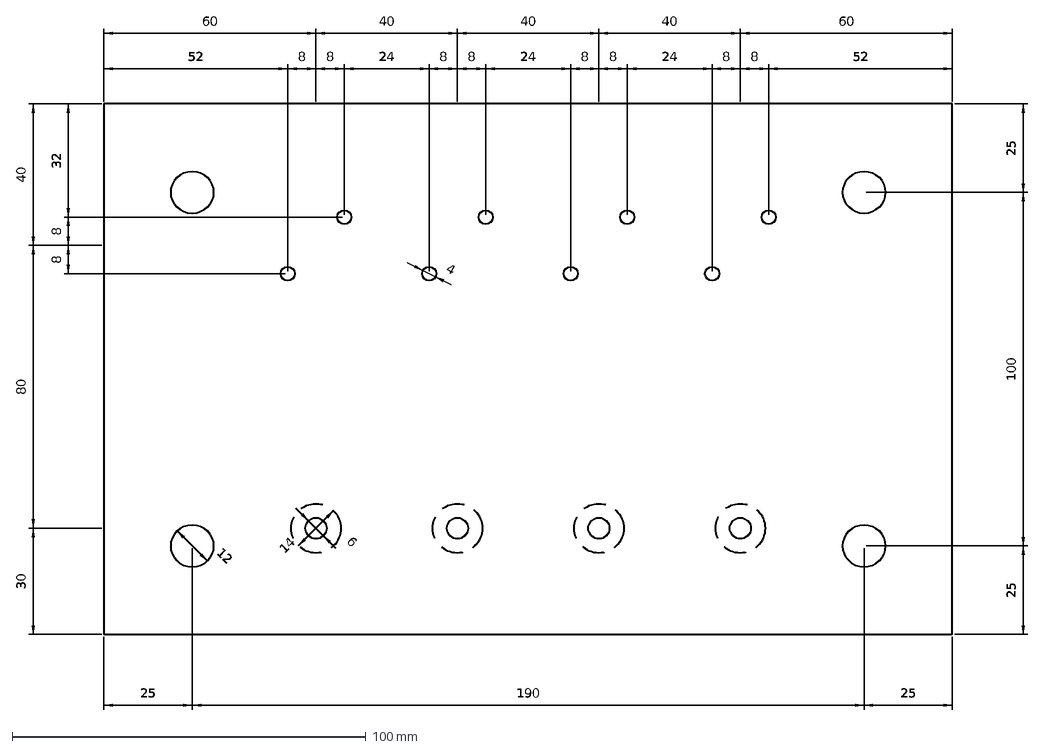
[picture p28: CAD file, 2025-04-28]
software/u8g2-master/sys/arduino/u8g2_full_buffer/SwitchBox/board.dxf
60
40
52
8
24
80
30
32
25
100
190
4
12
6
14

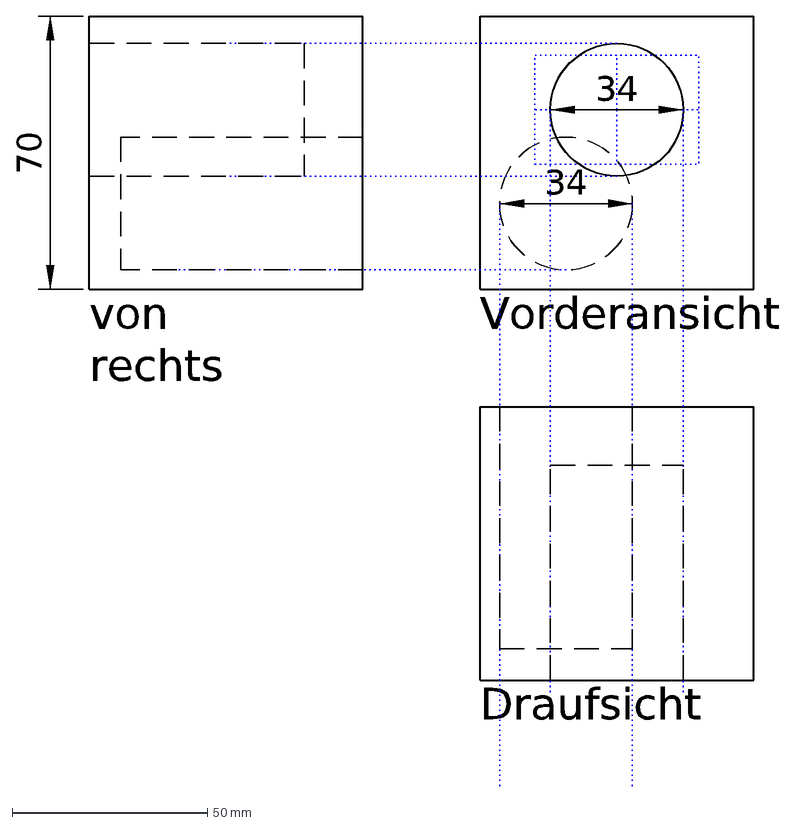
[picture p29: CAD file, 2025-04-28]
software/u8g2-master/sys/arm/stm32l031x6/clock_cube.dxf
Draufsicht
Vorderansicht
von rechts
70
34

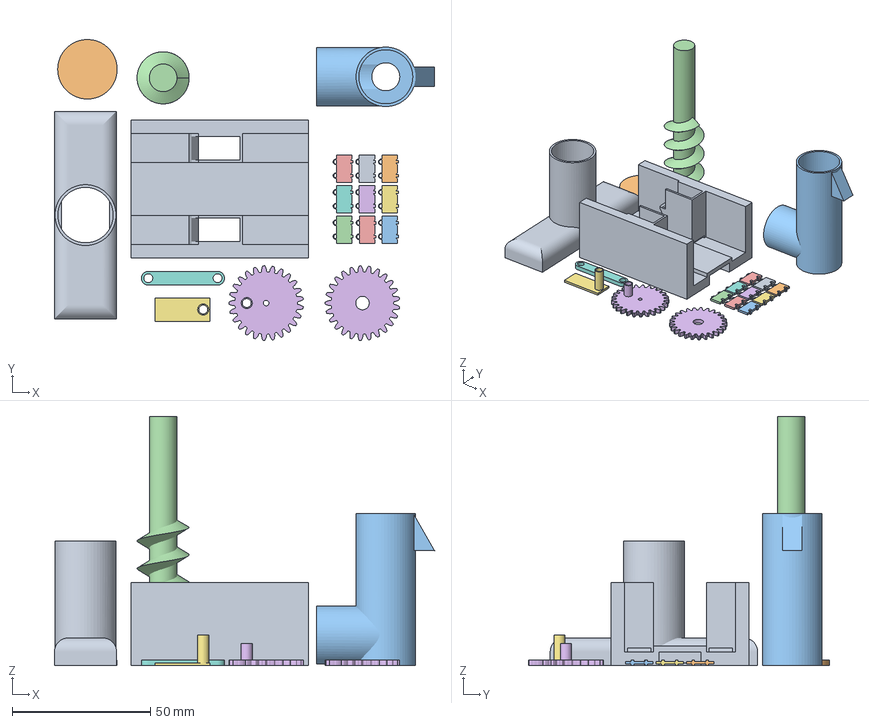
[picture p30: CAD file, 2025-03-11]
onshape/3mf files/Archi+pump.3mf
137.2 x 108.7 x 90.0 mm
pumpV2 part2.stl
visArchipart3 V2.stl
vis ArchiV2 part2.stl
visArchi V2 part1.stl
Part Studio 3 (1).stl x 9
gear V1.stl
bieleV1.stl
biele part2 V1.stl
rampe-food_cutV1.stl

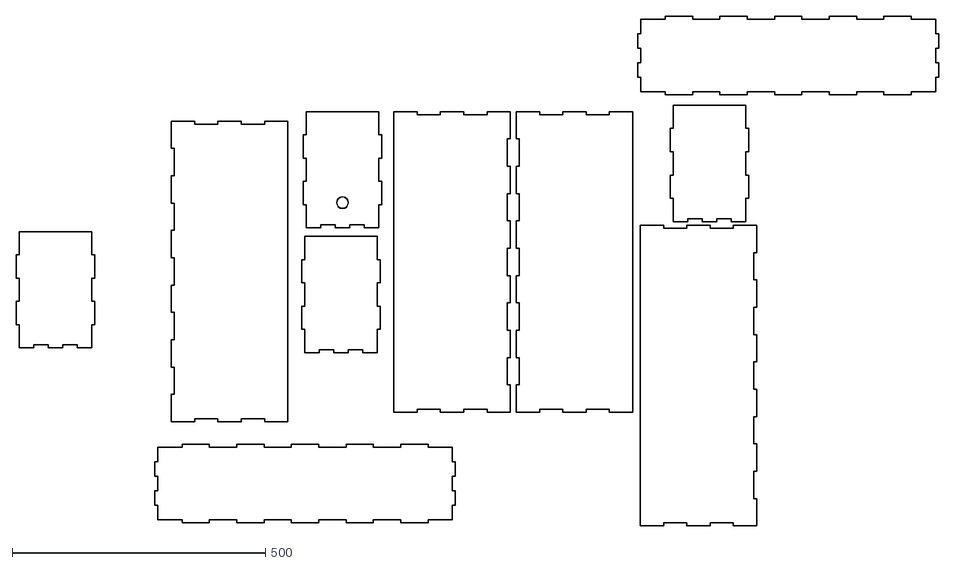
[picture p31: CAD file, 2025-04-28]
onshape/dxf files/2nd & 3rd tank.dxf
1821.6 x 1007.0

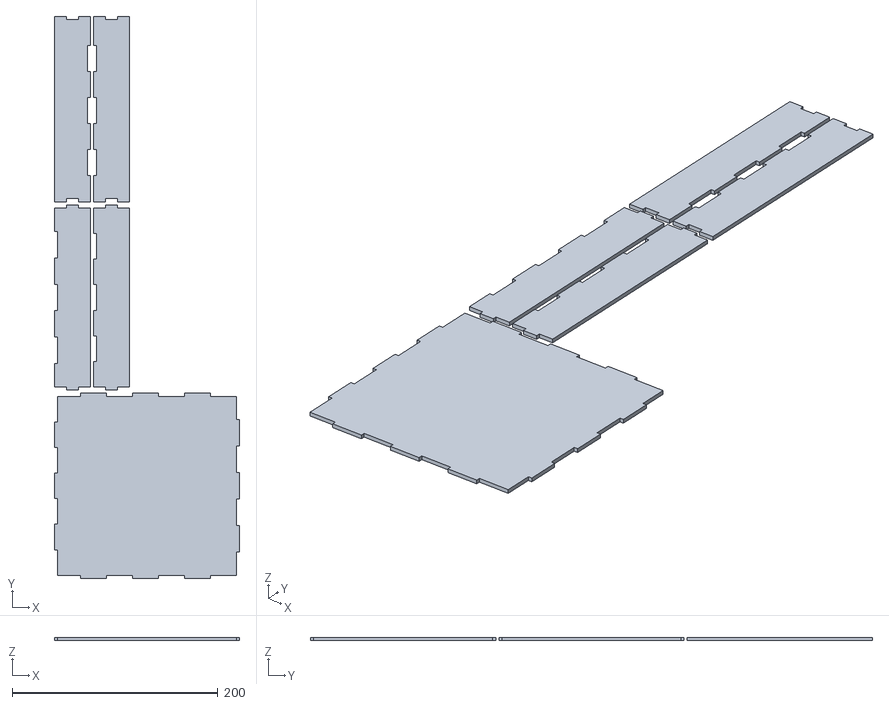
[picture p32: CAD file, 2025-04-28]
onshape/stl files/4th tank.stl
180.0 x 546.0 x 3.00

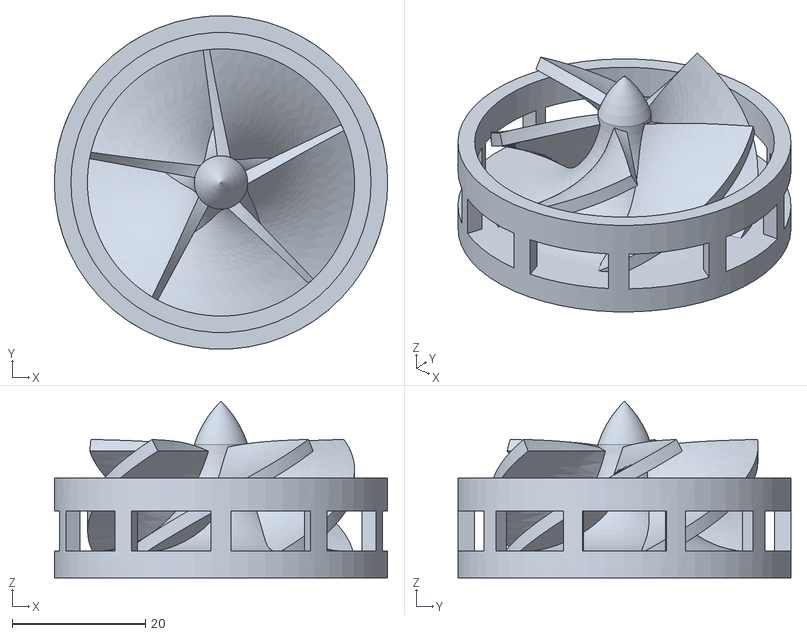
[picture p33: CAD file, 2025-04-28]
onshape/stl files/prototypes/vertical pump.stl
50.0 x 49.9 x 26.5

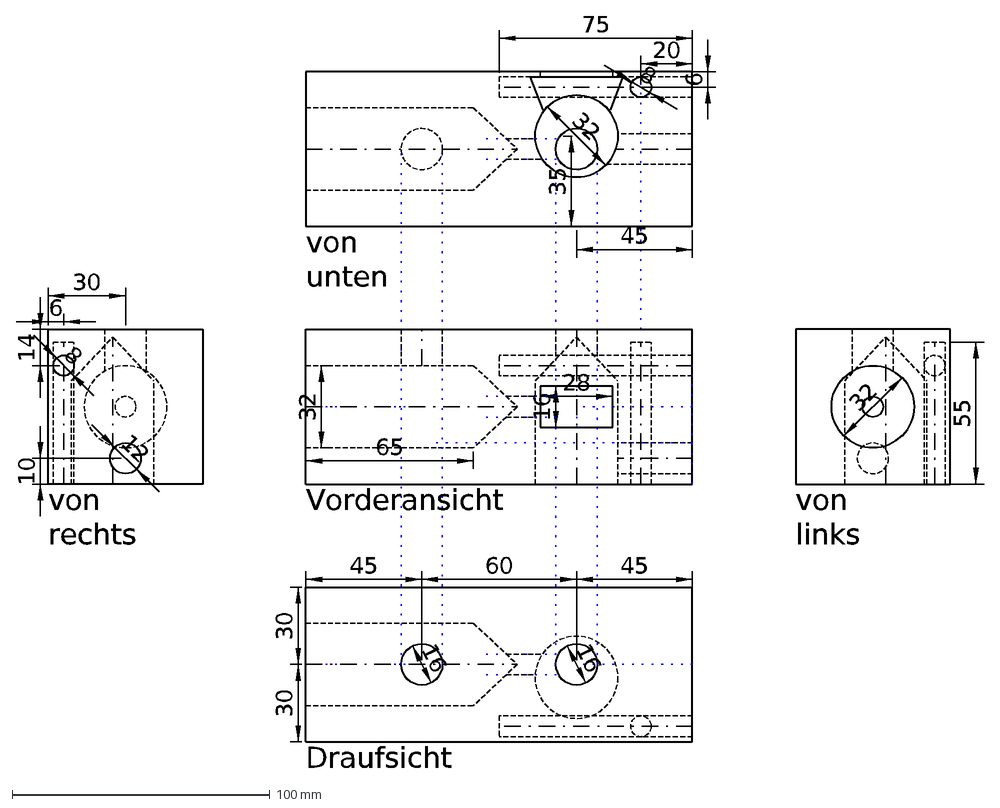
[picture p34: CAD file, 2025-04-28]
software/u8g2-master/sys/arm/stm32l031x6/clock.dxf
65
32
28
16
Draufsicht
Vorderansicht
von unten
von rechts
von links
14
6
45
60
30
20
8
35
75
55
10
12

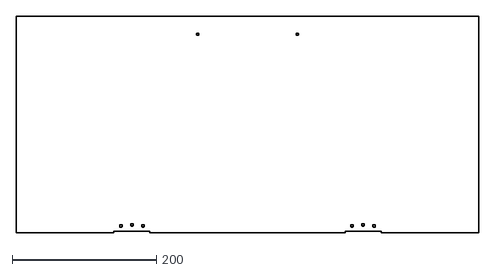
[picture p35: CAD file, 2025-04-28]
onshape/dxf files/face 2 (1).dxf
641.0 x 300.5

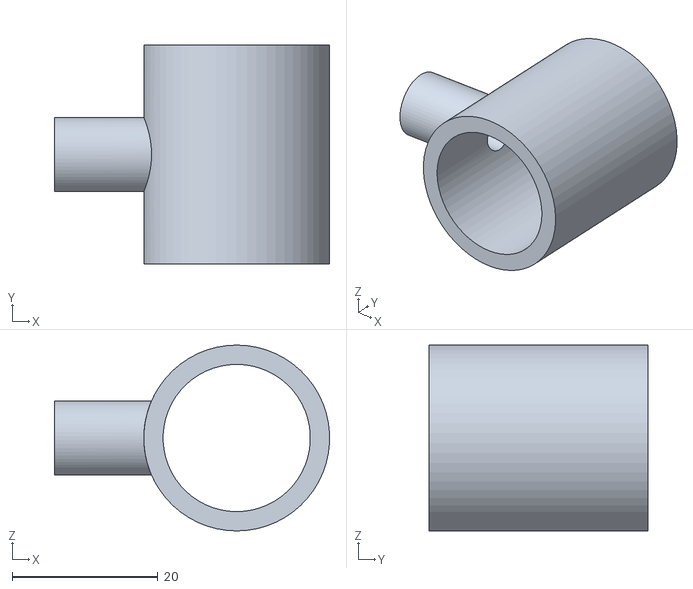
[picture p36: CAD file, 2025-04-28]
onshape/stl files/pipe connection model 2.stl
37.7 x 30.0 x 25.5

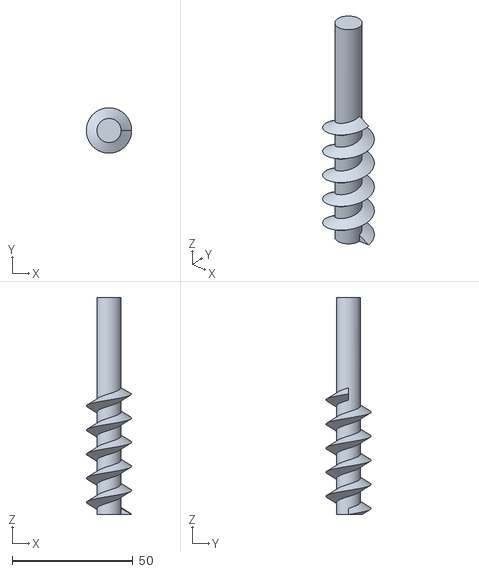
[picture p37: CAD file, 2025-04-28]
onshape/stl files/prototypes/pump part 1.stl
18.8 x 18.8 x 90.0

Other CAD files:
onshape/3mf files/filtreV3.3mf
onshape/3mf files/cacheV1.3mf
software/u8g2-master/sys/arm/stm32l031x6/clock_2.dxf
onshape/dxf files/Left & Right (1).dxf
onshape/dxf files/4th tank.dxf
onshape/dxf files/Top & Bot.dxf
onshape/dxf files/face 1.dxf
onshape/dxf files/floor.dxf
onshape/stl files/2nd tank (used water).stl
onshape/stl files/3rd tank (unused water).stl
onshape/stl files/Arms.stl
onshape/stl files/PCB protector.stl
onshape/stl files/aluminium profile.stl
onshape/stl files/drops test v2.stl
onshape/stl files/floor.stl
onshape/stl files/food entry.stl
onshape/stl files/furnitures walls.stl
onshape/stl files/gear test.stl
onshape/stl files/handle.stl
onshape/stl files/light v2.stl
onshape/stl files/motor ring.stl
onshape/stl files/pipe bloc.stl
onshape/stl files/pipe connection model 1.stl
onshape/stl files/prototypes/drops test v1.stl
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

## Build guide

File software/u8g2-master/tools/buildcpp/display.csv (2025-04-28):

# 1. device name
# 2. pinset
# 3. constructor name w/o prefix
u8x8_d_ssd1306_128x64_noname | 4WSWSPI | SSD1306_128X64_4W_SW_SPI
u8x8_d_ssd1306_128x64_noname | 4WHWSPI | SSD1306_128X64_4W_HW_SPI
u8x8_d_ssd1306_128x64_noname | 3WSWSPI | SSD1306_128X64_3W_SW_SPI
u8x8_d_ssd1306_128x64_noname | SSDSWI2C | SSD1306_128X64_SW_I2C
u8x8_d_ssd1306_128x64_noname | 6800 | SSD1306_128X64_6800
u8x8_d_ssd1306_128x64_noname | 8080 | SSD1306_128X64_8080

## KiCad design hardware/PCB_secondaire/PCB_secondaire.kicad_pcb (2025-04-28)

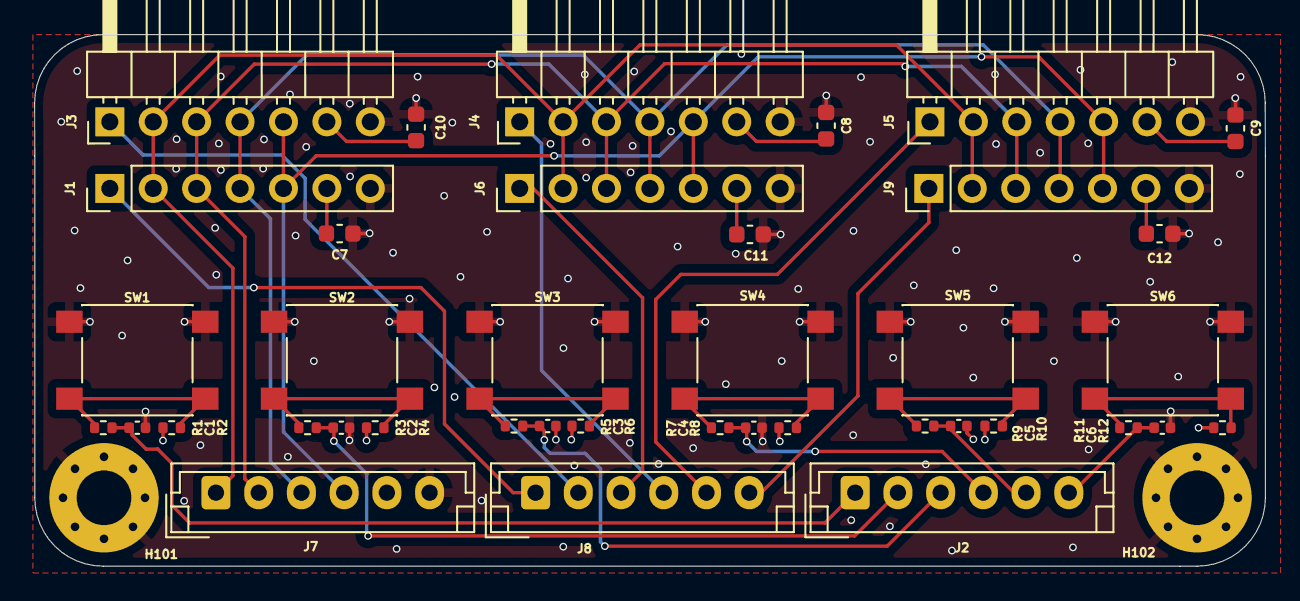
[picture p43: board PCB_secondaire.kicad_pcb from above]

Board: 4 copper layers, 72.0 x 31.1 mm, 41 parts (0 on the bottom side), 24 nets.

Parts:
C1, C2, C3, C4, C5, C6: 10n; C_0402_1005Metric
C7, C8, C9, C10, C11, C12: 1u; C_0603_1608Metric
H101, H102: MountingHole_Pad; MountingHole_3.2mm_M3_Pad_Via
J1, J6, J9: Conn_01x07; PinHeader_1x07_P2.54mm_Vertical
J2, J7, J8: Conn_01x06; JST_EH_B6B-EH-A_1x06_P2.50mm_Vertical
J3, J4, J5: Conn_01x07; PinHeader_1x07_P2.54mm_Horizontal
R1, R2, R3, R4, R5, R6, R7, R8, R9, R10, R11, R12: 10k; R_0402_1005Metric
SW1, SW2, SW3, SW4, SW5, SW6: SW_SPST; SW_Push_1P1T_NO_6x6mm_H9.5mm

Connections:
+3.3V: C7.2, C8.2, C9.2, C10.2, C11.2, C12.2, J1.6, J3.6, J4.6, J5.6, J6.6, J7.5, J9.6, R2.1, R4.1, R6.1, R8.1, R10.1, R12.1
/SPI_CS_1: J1.1, J8.1
/SPI_CS_2: J3.1, J8.2
/SPI_CS_3: J6.1, J8.3
/SPI_CS_4: J4.1, J8.4
/SPI_CS_5: J5.1, J8.5
/SPI_CS_6: J8.6, J9.1
/SPI_D/C: J1.2, J3.2, J4.2, J5.2, J6.2, J7.1, J9.2
/SPI_MOSI: J1.4, J3.4, J4.4, J5.4, J6.4, J7.3, J9.4
/SPI_RES: J1.3, J3.3, J4.3, J5.3, J6.3, J7.2, J9.3
/SPI_SCK: J1.5, J3.5, J4.5, J5.5, J6.5, J7.4, J9.5
BTN_1: C1.1, J2.1, R1.2
BTN_2: C2.1, J2.2, R3.2
BTN_3: C3.1, J2.3, R5.2
BTN_4: C4.1, J2.4, R7.2
BTN_5: C5.1, J2.5, R9.2
BTN_6: C6.1, J2.6, R11.2
GND: C1.2, C2.2, C3.2, C4.2, C5.2, C6.2, C7.1, C8.1, C9.1, C10.1, C11.1, C12.1, H101.1, H102.1, J1.7, J3.7, J4.7, J5.7, J6.7, J7.6, J9.7, SW1.2 (B), SW2.2 (B), SW3.2 (B), SW4.2 (B), SW5.2 (B), SW6.2 (B)
unnamed: R1.1, R2.2, SW1.1 (A)
unnamed: R3.1, R4.2, SW2.1 (A)
unnamed: R5.1, R6.2, SW3.1 (A)
unnamed: R7.1, R8.2, SW4.1 (A)
unnamed: R9.1, R10.2, SW5.1 (A)
unnamed: R11.1, R12.2, SW6.1 (A)

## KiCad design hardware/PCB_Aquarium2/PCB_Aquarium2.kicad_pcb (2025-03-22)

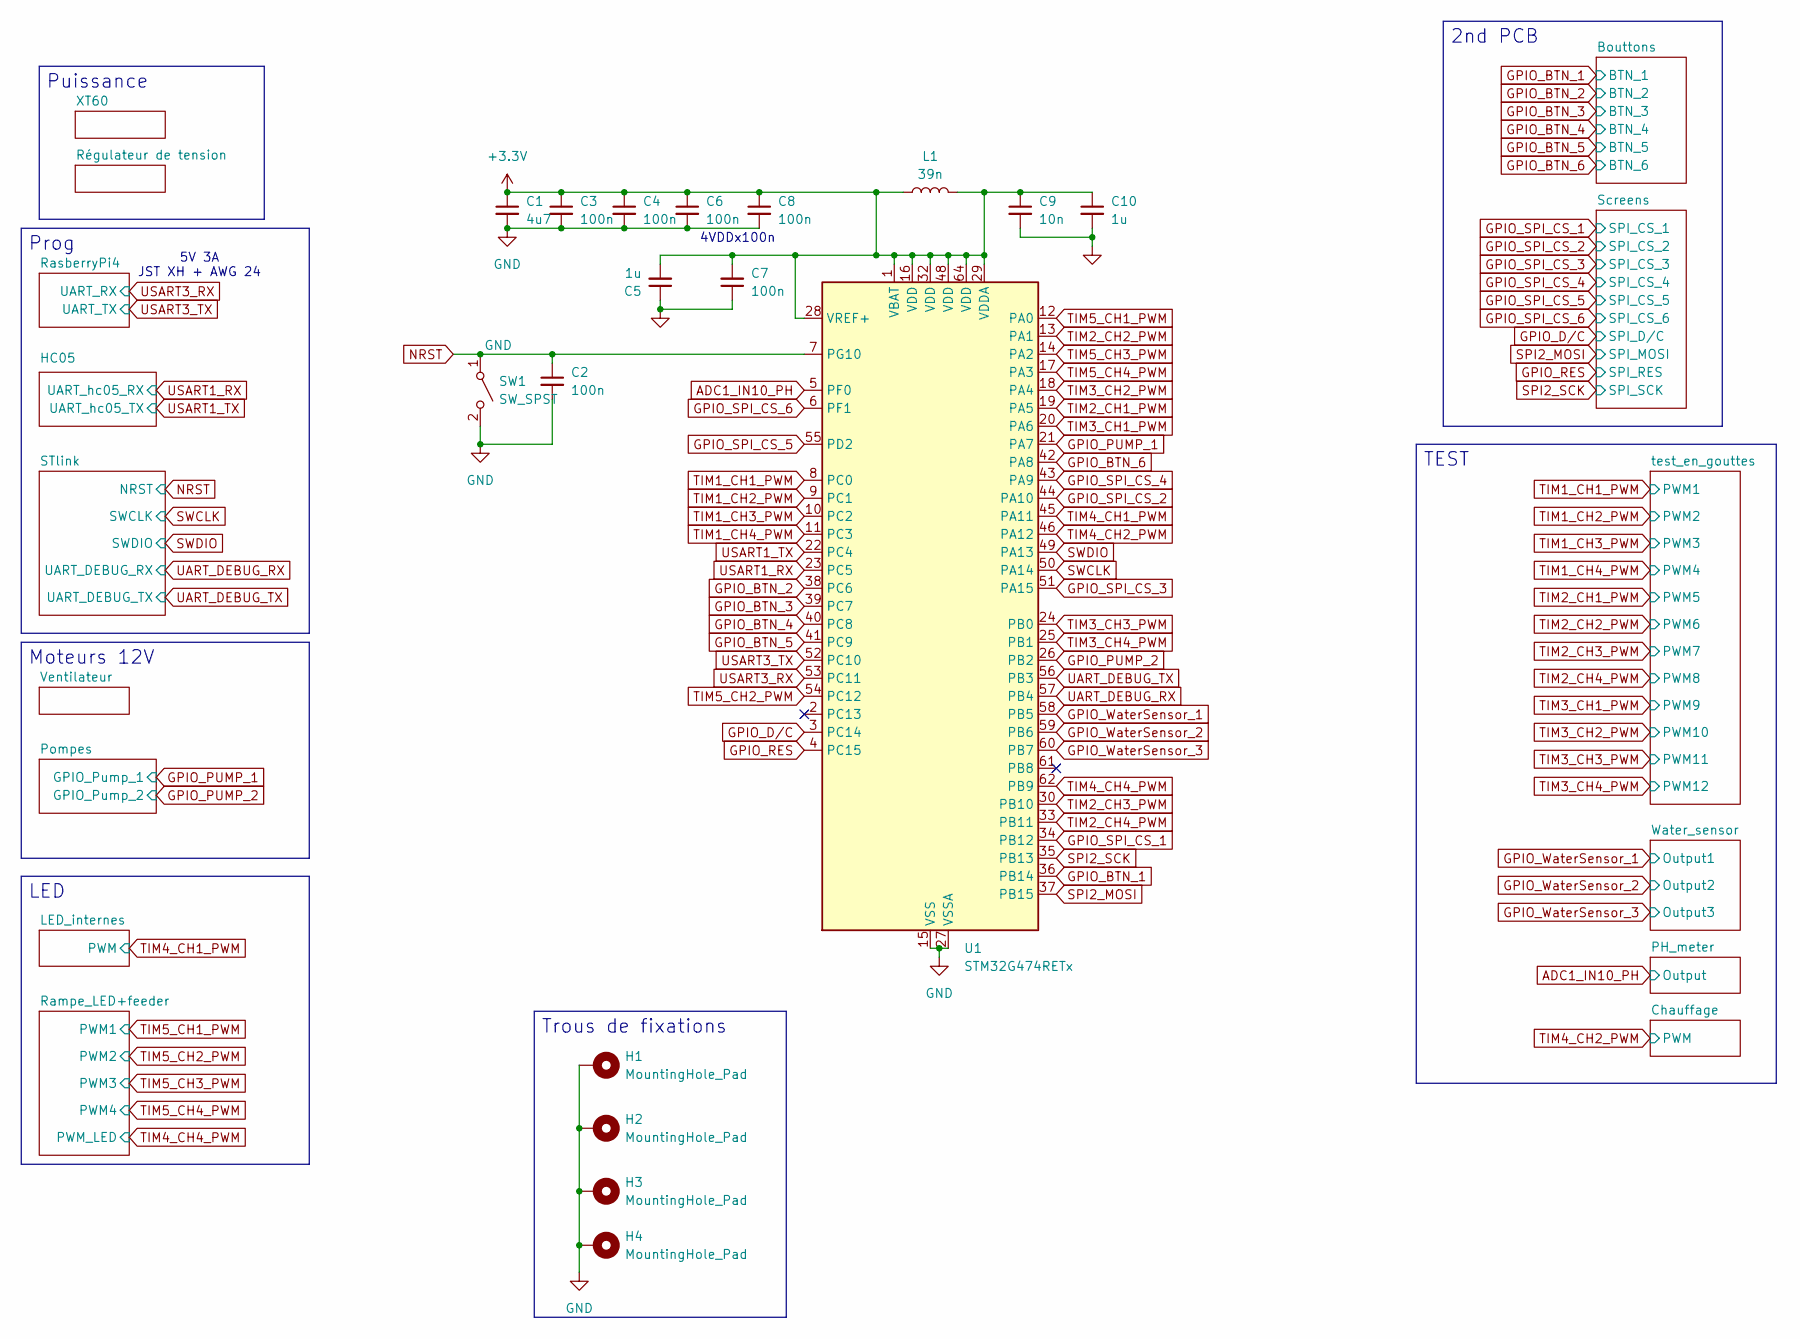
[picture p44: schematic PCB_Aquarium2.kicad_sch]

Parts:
C1: 4u7; C_0603_1608Metric
C2, C3, C4, C6, C7, C8: 100n; C_0402_1005Metric
C5, C10: 1u; C_0603_1608Metric
C9: 10n; C_0402_1005Metric
H1, H2, H3, H4: MountingHole_Pad; MountingHole_3.2mm_M3_Pad_Via
L1: 39n; L_0805_2012Metric
SW1: SW_SPST; SW_Push_1P1T_NO_6x6mm_H9.5mm
U1: STM32G474RETx; LQFP-64_10x10mm_P0.5mm

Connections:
+3.3V: C1.1, C3.1, C4.1, C5.2, C6.1, C7.2, C8.1, C9.1, C10.1, L1.1, L1.2, U1.1 (VBAT), U1.16 (VDD), U1.28 (VREF+), U1.29 (VDDA), U1.32 (VDD), U1.48 (VDD), U1.64 (VDD); also elsewhere on the board
ADC1_IN10_PH: U1.5 (PF0); also elsewhere on the board
GND: C1.2, C2.2, C3.2, C4.2, C5.1, C6.2, C7.1, C8.2, C9.2, C10.2, H1.1, H2.1, H3.1, H4.1, SW1.2 (B), U1.15 (VSS), U1.27 (VSSA), U1.31 (VSS), U1.47 (VSS), U1.63 (VSS); also elsewhere on the board
GPIO_BTN_1: U1.36 (PB14); also elsewhere on the board
GPIO_BTN_2: U1.38 (PC6); also elsewhere on the board
GPIO_BTN_3: U1.39 (PC7); also elsewhere on the board
GPIO_BTN_4: U1.40 (PC8); also elsewhere on the board
GPIO_BTN_5: U1.41 (PC9); also elsewhere on the board
GPIO_BTN_6: U1.42 (PA8); also elsewhere on the board
GPIO_D/C: U1.3 (PC14); also elsewhere on the board
GPIO_PUMP_1: U1.21 (PA7); also elsewhere on the board
GPIO_PUMP_2: U1.26 (PB2); also elsewhere on the board
GPIO_RES: U1.4 (PC15); also elsewhere on the board
GPIO_SPI_CS_1: U1.34 (PB12); also elsewhere on the board
GPIO_SPI_CS_2: U1.44 (PA10); also elsewhere on the board
GPIO_SPI_CS_3: U1.51 (PA15); also elsewhere on the board
GPIO_SPI_CS_4: U1.43 (PA9); also elsewhere on the board
GPIO_SPI_CS_5: U1.55 (PD2); also elsewhere on the board
GPIO_SPI_CS_6: U1.6 (PF1); also elsewhere on the board
GPIO_WaterSensor_1: U1.58 (PB5); also elsewhere on the board
GPIO_WaterSensor_2: U1.59 (PB6); also elsewhere on the board
GPIO_WaterSensor_3: U1.60 (PB7); also elsewhere on the board
NRST: C2.1, SW1.1 (A), U1.7 (PG10); also elsewhere on the board
SPI2_MOSI: U1.37 (PB15); also elsewhere on the board
SPI2_SCK: U1.35 (PB13); also elsewhere on the board
SWCLK: U1.50 (PA14); also elsewhere on the board
SWDIO: U1.49 (PA13); also elsewhere on the board
TIM1_CH1_PWM: U1.8 (PC0); also elsewhere on the board
TIM1_CH2_PWM: U1.9 (PC1); also elsewhere on the board
TIM1_CH3_PWM: U1.10 (PC2); also elsewhere on the board
TIM1_CH4_PWM: U1.11 (PC3); also elsewhere on the board
TIM2_CH1_PWM: U1.19 (PA5); also elsewhere on the board
TIM2_CH2_PWM: U1.13 (PA1); also elsewhere on the board
TIM2_CH3_PWM: U1.30 (PB10); also elsewhere on the board
TIM2_CH4_PWM: U1.33 (PB11); also elsewhere on the board
TIM3_CH1_PWM: U1.20 (PA6); also elsewhere on the board
TIM3_CH2_PWM: U1.18 (PA4); also elsewhere on the board
TIM3_CH3_PWM: U1.24 (PB0); also elsewhere on the board
TIM3_CH4_PWM: U1.25 (PB1); also elsewhere on the board
TIM4_CH1_PWM: U1.45 (PA11); also elsewhere on the board
TIM4_CH2_PWM: U1.46 (PA12); also elsewhere on the board
TIM4_CH4_PWM: U1.62 (PB9); also elsewhere on the board
TIM5_CH1_PWM: U1.12 (PA0); also elsewhere on the board
TIM5_CH2_PWM: U1.54 (PC12); also elsewhere on the board
TIM5_CH3_PWM: U1.14 (PA2); also elsewhere on the board
TIM5_CH4_PWM: U1.17 (PA3); also elsewhere on the board
UART_DEBUG_RX: U1.57 (PB4); also elsewhere on the board
UART_DEBUG_TX: U1.56 (PB3); also elsewhere on the board
USART1_RX: U1.23 (PC5); also elsewhere on the board
USART1_TX: U1.22 (PC4); also elsewhere on the board
USART3_RX: U1.53 (PC11); also elsewhere on the board
USART3_TX: U1.52 (PC10); also elsewhere on the board

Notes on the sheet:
5V 3A JST XH + AWG 24
4VDDx100n
TEST
Puissance
LED
2nd PCB
Moteurs 12V
Trous de fixations
Prog

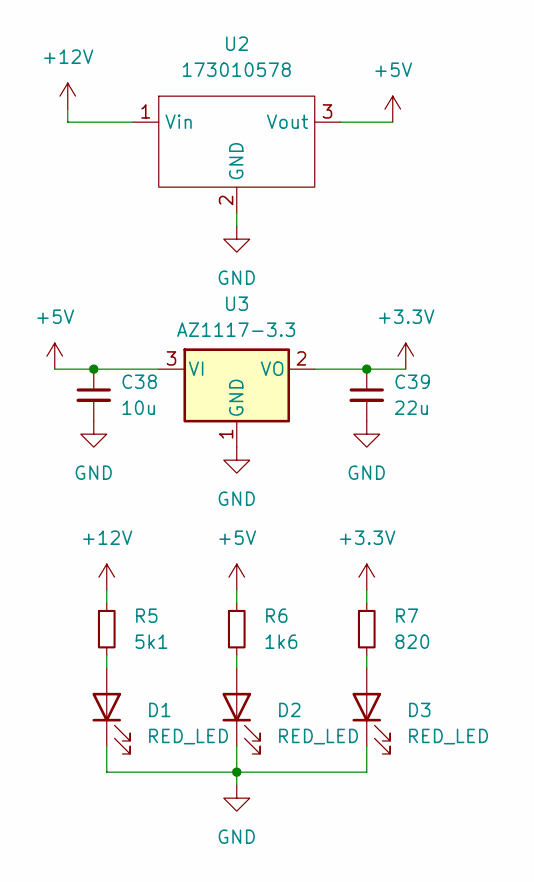
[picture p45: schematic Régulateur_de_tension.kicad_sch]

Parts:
C38: 10u; C_0603_1608Metric
C39: 22u; C_Elec_5x5.4
D1, D2, D3: RED_LED; LED_0603_1608Metric; MPN 150060RS55040
R5: 5k1; R_0402_1005Metric
R6: 1k6; R_0402_1005Metric
R7: 820; R_0402_1005Metric
U2: 173010578; 173010542; MPN 173010578
U3: AZ1117-3.3; SOT-223-3_TabPin2; MPN AZ1117CH2-3.3TRG1

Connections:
+3.3V: C39.1, R7.1, U3.2 (VO); also elsewhere on the board
+5V: C38.1, R6.1, U2.3 (Vout), U3.3 (VI); also elsewhere on the board
+12V: R5.1, U2.1 (Vin); also elsewhere on the board
GND: C38.2, C39.2, D1.1 (K), D2.1 (K), D3.1 (K), U2.2 (GND), U3.1 (GND); also elsewhere on the board
unnamed: D1.2 (A), R5.2
unnamed: D2.2 (A), R6.2
unnamed: D3.2 (A), R7.2

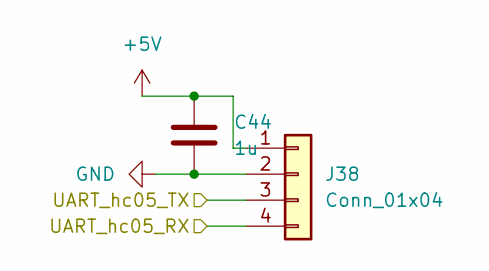
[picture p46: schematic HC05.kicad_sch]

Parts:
C44: 1u; C_0603_1608Metric
J38: Conn_01x04; JST_EH_B4B-EH-A_1x04_P2.50mm_Vertical

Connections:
+5V: C44.2, J38.1; also elsewhere on the board
GND: C44.1, J38.2; also elsewhere on the board
USART1_RX: J38.4; also elsewhere on the board
USART1_TX: J38.3; also elsewhere on the board

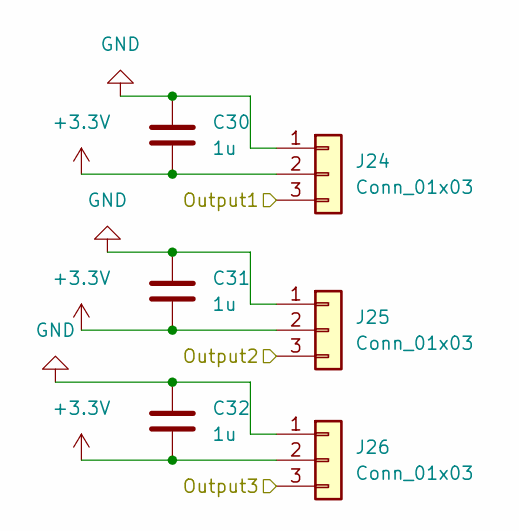
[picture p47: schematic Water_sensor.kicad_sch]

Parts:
C30, C31, C32: 1u; C_0603_1608Metric
J24, J25, J26: Conn_01x03; JST_EH_B3B-EH-A_1x03_P2.50mm_Vertical

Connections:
+3.3V: C30.1, C31.1, C32.1, J24.2, J25.2, J26.2; also elsewhere on the board
GND: C30.2, C31.2, C32.2, J24.1, J25.1, J26.1; also elsewhere on the board
GPIO_WaterSensor_1: J24.3; also elsewhere on the board
GPIO_WaterSensor_2: J25.3; also elsewhere on the board
GPIO_WaterSensor_3: J26.3; also elsewhere on the board

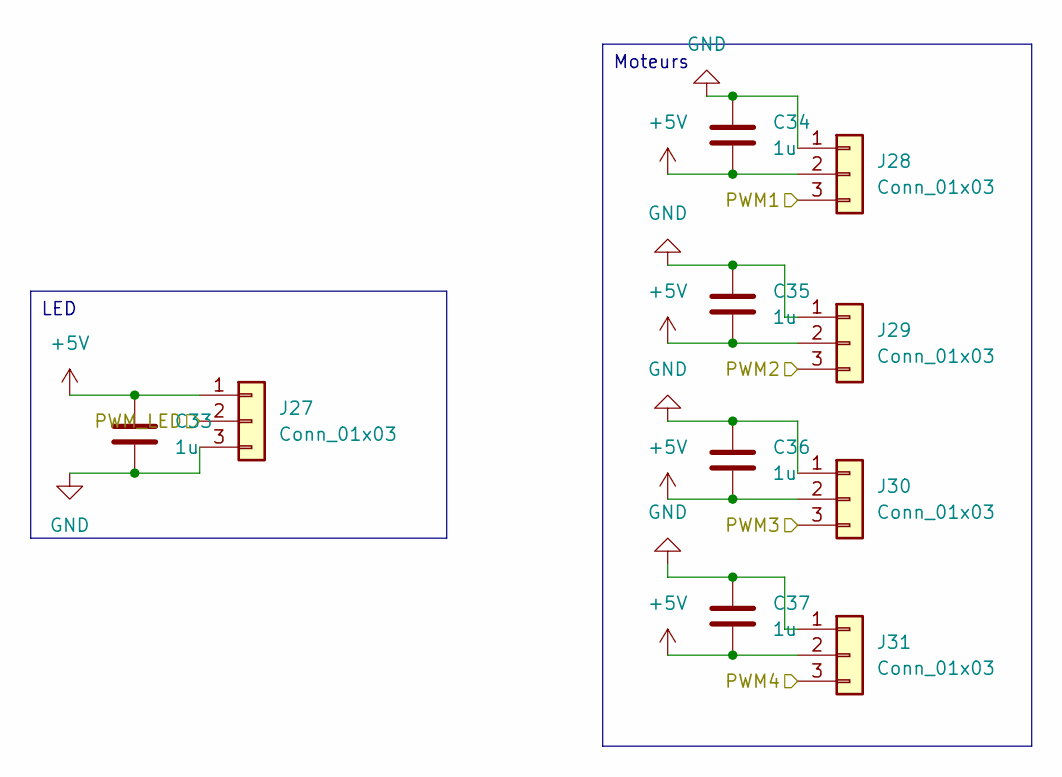
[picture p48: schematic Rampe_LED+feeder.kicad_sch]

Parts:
C33, C34, C35, C36, C37: 1u; C_0603_1608Metric
J27, J28, J29, J30, J31: Conn_01x03; JST_EH_B3B-EH-A_1x03_P2.50mm_Vertical

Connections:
+5V: C33.2, C34.1, C35.1, C36.1, C37.1, J27.1, J28.2, J29.2, J30.2, J31.2; also elsewhere on the board
GND: C33.1, C34.2, C35.2, C36.2, C37.2, J27.3, J28.1, J29.1, J30.1, J31.1; also elsewhere on the board
TIM4_CH4_PWM: J27.2; also elsewhere on the board
TIM5_CH1_PWM: J28.3; also elsewhere on the board
TIM5_CH2_PWM: J29.3; also elsewhere on the board
TIM5_CH3_PWM: J30.3; also elsewhere on the board
TIM5_CH4_PWM: J31.3; also elsewhere on the board

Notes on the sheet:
LED
Moteurs

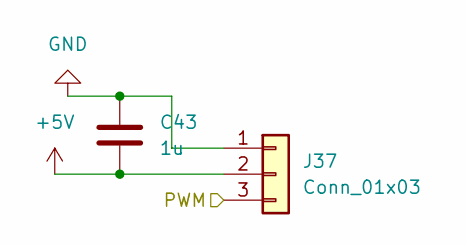
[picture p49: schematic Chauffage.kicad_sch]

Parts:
C43: 1u; C_0603_1608Metric
J37: Conn_01x03; JST_EH_B3B-EH-A_1x03_P2.50mm_Vertical

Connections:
+5V: C43.1, J37.2; also elsewhere on the board
GND: C43.2, J37.1; also elsewhere on the board
TIM4_CH2_PWM: J37.3; also elsewhere on the board

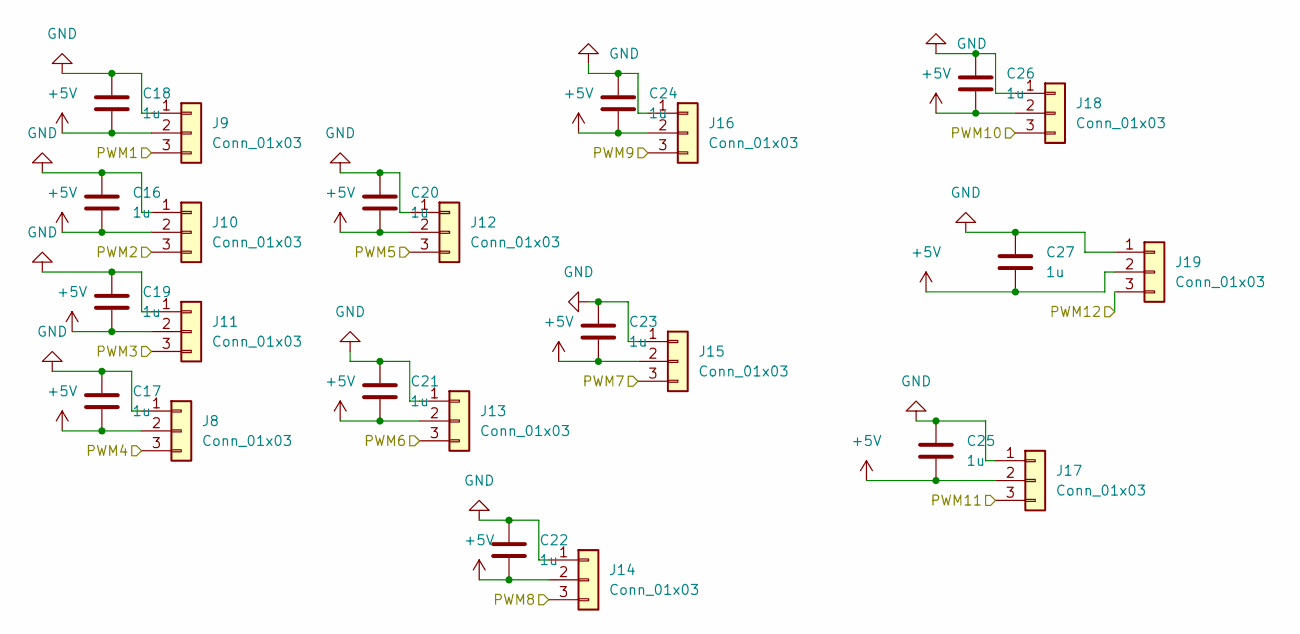
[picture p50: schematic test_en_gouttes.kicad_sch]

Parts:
C16, C17, C18, C19, C20, C21, C22, C23, C24, C25, C26, C27: 1u; C_0603_1608Metric
J8, J9, J10, J11, J12, J13, J14, J15, J16, J17, J18, J19: Conn_01x03; JST_EH_B3B-EH-A_1x03_P2.50mm_Vertical

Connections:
+5V: C16.1, C17.1, C18.1, C19.1, C20.1, C21.1, C22.1, C23.1, C24.1, C25.2, C26.2, C27.1, J8.2, J9.2, J10.2, J11.2, J12.2, J13.2, J14.2, J15.2, J16.2, J17.2, J18.2, J19.2; also elsewhere on the board
GND: C16.2, C17.2, C18.2, C19.2, C20.2, C21.2, C22.2, C23.2, C24.2, C25.1, C26.1, C27.2, J8.1, J9.1, J10.1, J11.1, J12.1, J13.1, J14.1, J15.1, J16.1, J17.1, J18.1, J19.1; also elsewhere on the board
TIM1_CH1_PWM: J9.3; also elsewhere on the board
TIM1_CH2_PWM: J10.3; also elsewhere on the board
TIM1_CH3_PWM: J11.3; also elsewhere on the board
TIM1_CH4_PWM: J8.3; also elsewhere on the board
TIM2_CH1_PWM: J12.3; also elsewhere on the board
TIM2_CH2_PWM: J13.3; also elsewhere on the board
TIM2_CH3_PWM: J15.3; also elsewhere on the board
TIM2_CH4_PWM: J14.3; also elsewhere on the board
TIM3_CH1_PWM: J16.3; also elsewhere on the board
TIM3_CH2_PWM: J18.3; also elsewhere on the board
TIM3_CH3_PWM: J17.3; also elsewhere on the board
TIM3_CH4_PWM: J19.3; also elsewhere on the board

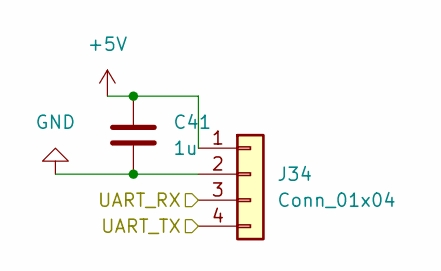
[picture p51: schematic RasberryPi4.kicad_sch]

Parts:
C41: 1u; C_0603_1608Metric
J34: Conn_01x04; JST_XH_B4B-XH-A_1x04_P2.50mm_Vertical

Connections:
+5V: C41.2, J34.1; also elsewhere on the board
GND: C41.1, J34.2; also elsewhere on the board
USART3_RX: J34.3; also elsewhere on the board
USART3_TX: J34.4; also elsewhere on the board

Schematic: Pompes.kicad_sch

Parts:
C28, C29: 1u; C_0603_1608Metric
J20, J21, J22, J23: Conn_01x02; JST_EH_B2B-EH-A_1x02_P2.50mm_Vertical
Q1, Q2: NMOS; SOT-23; MPN SQ2310ES
R1, R3: 1k; R_0402_1005Metric
R2, R4: 10k; R_0402_1005Metric

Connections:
+12V: C28.2, C29.1, J20.1, J21.1, J22.1, J23.1; also elsewhere on the board
GND: C28.1, C29.2, J22.2, J23.2, Q1.3 (S), Q2.3 (S), R2.2, R4.2; also elsewhere on the board
GPIO_PUMP_1: R1.2; also elsewhere on the board
GPIO_PUMP_2: R3.2; also elsewhere on the board
unnamed: J20.2, Q1.1 (D)
unnamed: J21.2, Q2.1 (D)
unnamed: Q1.2 (G), R1.1, R2.1
unnamed: Q2.2 (G), R3.1, R4.1

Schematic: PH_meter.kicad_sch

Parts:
C11: 1u; C_0603_1608Metric
J1: Conn_01x03; JST_EH_B3B-EH-A_1x03_P2.50mm_Vertical

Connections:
+5V: C11.1, J1.2; also elsewhere on the board
ADC1_IN10_PH: J1.3; also elsewhere on the board
GND: C11.2, J1.1; also elsewhere on the board

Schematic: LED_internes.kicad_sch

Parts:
C42: 1u; C_0603_1608Metric
J36: Conn_01x03; JST_EH_B3B-EH-A_1x03_P2.50mm_Vertical

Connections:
+5V: C42.2, J36.1; also elsewhere on the board
GND: C42.1, J36.3; also elsewhere on the board
TIM4_CH1_PWM: J36.2; also elsewhere on the board

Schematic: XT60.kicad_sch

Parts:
J33: Conn_01x02; AMASS_XT60-M_1x02_P7.20mm_Vertical
SW2: SW_SPDT; 472123010111; MPN 472123010111

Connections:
+12V: SW2.1 (A); also elsewhere on the board
GND: J33.1; also elsewhere on the board
unnamed: J33.2, SW2.2 (B)

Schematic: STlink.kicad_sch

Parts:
J35: Conn_ST_STDC14; PinHeader_2x07_P1.27mm_Vertical_SMD; MPN STLINK-V3MINIE

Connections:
+3.3V: J35.3 (VCC); also elsewhere on the board
GND: J35.5 (GND), J35.7 (GND), J35.11 (GNDDetect); also elsewhere on the board
NRST: J35.12 (~RST); also elsewhere on the board
SWCLK: J35.6 (JCLK/SWCLK); also elsewhere on the board
SWDIO: J35.4 (JTMS/SWDIO); also elsewhere on the board
UART_DEBUG_RX: J35.13 (VCP_RX); also elsewhere on the board
UART_DEBUG_TX: J35.14 (VCP_TX); also elsewhere on the board

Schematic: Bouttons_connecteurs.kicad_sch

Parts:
J2: Conn_01x06; JST_EH_B6B-EH-A_1x06_P2.50mm_Vertical

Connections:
GPIO_BTN_1: J2.1; also elsewhere on the board
GPIO_BTN_2: J2.2; also elsewhere on the board
GPIO_BTN_3: J2.3; also elsewhere on the board
GPIO_BTN_4: J2.4; also elsewhere on the board
GPIO_BTN_5: J2.5; also elsewhere on the board
GPIO_BTN_6: J2.6; also elsewhere on the board

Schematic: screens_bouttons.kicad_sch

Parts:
C15: 1u; C_0603_1608Metric
J6, J7: Conn_01x06; JST_EH_B6B-EH-A_1x06_P2.50mm_Vertical

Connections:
+3.3V: C15.2, J6.5; also elsewhere on the board
GND: C15.1, J6.6; also elsewhere on the board
GPIO_D/C: J6.1; also elsewhere on the board
GPIO_RES: J6.2; also elsewhere on the board
GPIO_SPI_CS_1: J7.1; also elsewhere on the board
GPIO_SPI_CS_2: J7.2; also elsewhere on the board
GPIO_SPI_CS_3: J7.3; also elsewhere on the board
GPIO_SPI_CS_4: J7.4; also elsewhere on the board
GPIO_SPI_CS_5: J7.5; also elsewhere on the board
GPIO_SPI_CS_6: J7.6; also elsewhere on the board
SPI2_MOSI: J6.3; also elsewhere on the board
SPI2_SCK: J6.4; also elsewhere on the board

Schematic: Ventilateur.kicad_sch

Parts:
C12: 1u; C_0603_1608Metric
J3: Conn_01x02; JST_EH_B2B-EH-A_1x02_P2.50mm_Vertical

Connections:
+12V: C12.2, J3.1; also elsewhere on the board
GND: C12.1, J3.2; also elsewhere on the board

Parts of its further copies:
C13, C14, C40: 1u; C_0603_1608Metric
J4, J5, J32: Conn_01x02; JST_EH_B2B-EH-A_1x02_P2.50mm_Vertical

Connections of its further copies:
+12V: C13.2, C14.2, C40.2, J4.1, J5.1, J32.1; also elsewhere on the board
GND: C13.1, C14.1, C40.1, J4.2, J5.2, J32.2; also elsewhere on the board

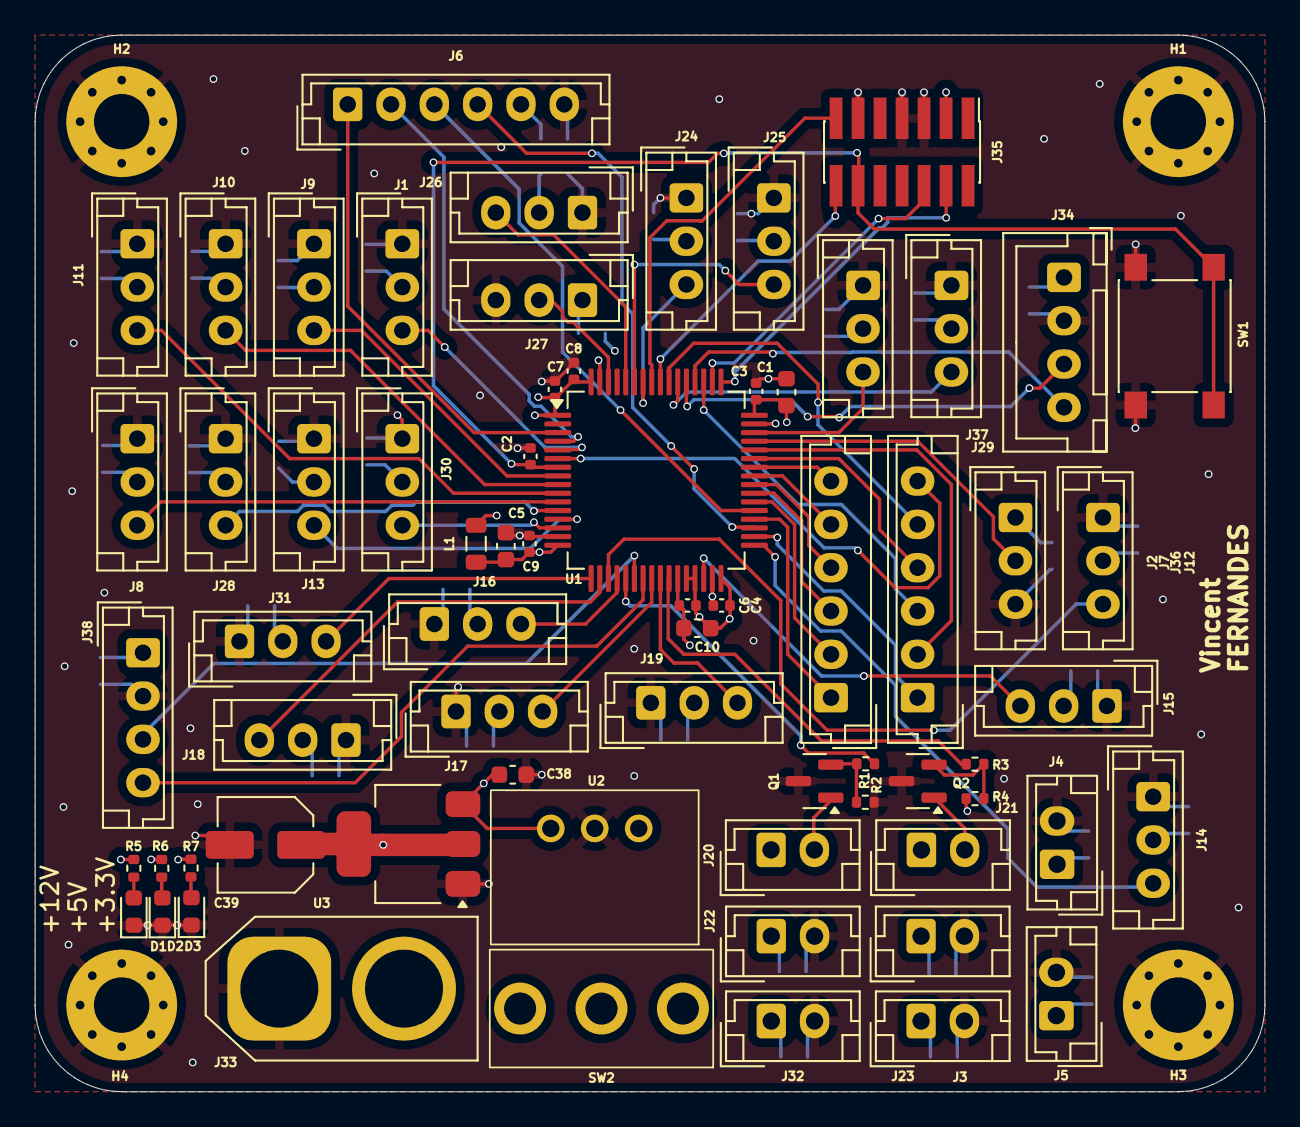
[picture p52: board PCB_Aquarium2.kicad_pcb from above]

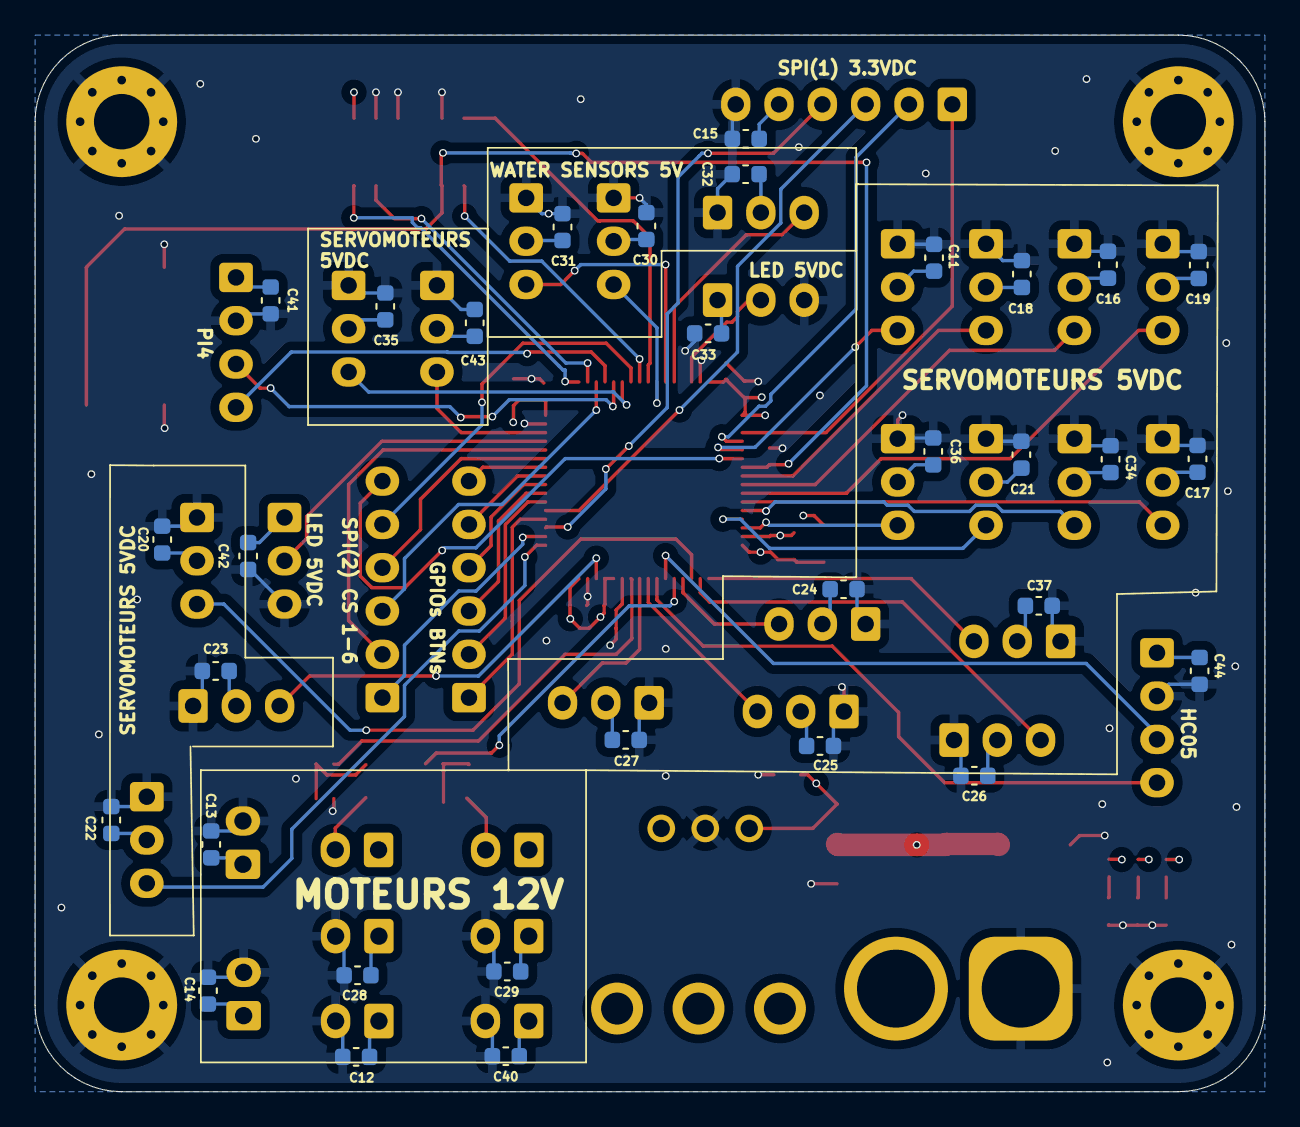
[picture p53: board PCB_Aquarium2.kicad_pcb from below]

Board: 4 copper layers, 71.0 x 61.0 mm, 104 parts (32 on the bottom side), 62 nets.

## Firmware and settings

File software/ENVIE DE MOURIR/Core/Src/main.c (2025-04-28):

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
/* Includes ------------------------------------------------------------------*/
#include "main.h"

/* USER CODE BEGIN Includes */
#include <stdio.h>

#include "stdio.h"
/* USER CODE END Includes */

/* USER CODE BEGIN PM */
char zz[10];
/* USER CODE END PM */

SPI_HandleTypeDef hspi2;

UART_HandleTypeDef huart1;
UART_HandleTypeDef huart2;

void SystemClock_Config(void);
static void MX_GPIO_Init(void);
static void MX_USART2_UART_Init(void);
static void MX_SPI2_Init(void);
static void MX_USART1_UART_Init(void);
/**
  * @brief  The application entry point.
  * @retval int
  */
int main(void)
{

  /* MCU Configuration--------------------------------------------------------*/

  /* Reset of all peripherals, Initializes the Flash interface and the Systick. */
  HAL_Init();

  /* Configure the system clock */
  SystemClock_Config();

  /* Initialize all configured peripherals */
  MX_GPIO_Init();
  MX_USART2_UART_Init();
  MX_SPI2_Init();
  MX_USART1_UART_Init();
  /* Infinite loop */
  /* USER CODE BEGIN WHILE */
  while (1)
  {
	  int boubou = HAL_GPIO_ReadPin(GPIOA, GPIO_PIN_10);
	  if(boubou == 0){
		  HAL_GPIO_WritePin(GPIOA, GPIO_PIN_5, 1);
		  HAL_Delay(500);
		  HAL_GPIO_WritePin(GPIOA, GPIO_PIN_5, 0);
		  HAL_Delay(500);
	  }

	  /*HAL_GPIO_WritePin(GPIOA, GPIO_PIN_5, 1);
	  HAL_Delay(500);
	  HAL_GPIO_WritePin(GPIOA, GPIO_PIN_5, 0);
	  HAL_Delay(500);*/
/*
	  int test = HAL_GPIO_ReadPin(GPIOC, GPIO_PIN_13);
	  if(test != 1){
		 HAL_GPIO_WritePin(GPIOA, GPIO_PIN_5, 1);
		 printf("Hello World ! \n\r");
	  }
	  else{
		  HAL_GPIO_WritePin(GPIOA, GPIO_PIN_5, 0);
	  }
	  HAL_Delay(500);
*/

    /* USER CODE END WHILE */

    /* USER CODE BEGIN 3 */
  }
  /* USER CODE END 3 */
}

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
/* USER CODE BEGIN 4 */
int _write(int file, char *ptr, int len)
{
  (void)file;
  int DataIdx;

  for (DataIdx = 0; DataIdx < len; DataIdx++)
  {
    ITM_SendChar(*ptr++);
  }
  return len;
}
/* USER CODE END 4 */
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


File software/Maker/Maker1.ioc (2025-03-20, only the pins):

Mcu.UserName=STM32G474RETx
PA0.Signal=S_TIM5_CH1
PA1.Signal=S_TIM2_CH2
PA10.Signal=GPIO_Output
PA11.Signal=S_TIM4_CH1
PA12.Signal=S_TIM4_CH2
PA13.Signal=SYS_JTMS-SWDIO
PA14.Signal=SYS_JTCK-SWCLK
PA15.Signal=GPIO_Output
PA2.Signal=S_TIM5_CH3
PA3.Signal=S_TIM5_CH4
PA4.Signal=S_TIM3_CH2
PA5.Signal=S_TIM2_CH1
PA6.Signal=S_TIM3_CH1
PA7.Signal=GPIO_Output
PA8.Signal=GPIO_Input
PA9.Signal=GPIO_Output
PB0.Signal=S_TIM3_CH3
PB1.Signal=S_TIM3_CH4
PB10.Signal=S_TIM2_CH3
PB11.Signal=S_TIM2_CH4
PB12.Signal=GPIO_Output
PB13.Signal=SPI2_SCK
PB14.Signal=GPIO_Input
PB15.Signal=SPI2_MOSI
PB2.Signal=GPIO_Output
PB3.Signal=USART2_TX
PB4.Signal=USART2_RX
PB5.Signal=GPIO_Input
PB6.Signal=GPIO_Input
PB7.Signal=GPIO_Input
PB9.Signal=S_TIM4_CH4
PC0.Signal=S_TIM1_CH1
PC1.Signal=S_TIM1_CH2
PC10.Signal=USART3_TX
PC11.Signal=USART3_RX
PC12.Signal=S_TIM5_CH2
PC13.Signal=GPIO_Input
PC14-OSC32_IN.Signal=GPIO_Output
PC15-OSC32_OUT.Signal=GPIO_Output
PC2.Signal=S_TIM1_CH3
PC3.Signal=S_TIM1_CH4
PC4.Signal=USART1_TX
PC5.Signal=USART1_RX
PC6.Signal=GPIO_Input
PC7.Signal=GPIO_Input
PC8.Signal=GPIO_Input
PC9.Signal=GPIO_Input
PD2.Signal=GPIO_Output
PF0-OSC_IN.Signal=ADC1_IN10
PF1-OSC_OUT.Signal=GPIO_Output

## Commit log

2025-03-17 PCBs V1
    [BTN.kicad_sch, Bouttons_connecteurs.kicad_sch, Chauffage.kicad_sch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]
2025-03-17 PCBs v2
    [PCB_Aquarium2.kicad_pcb, PCB_secondaire.kicad_pcb, PCB_secondaire.kicad_sch]
2025-03-17 PCBs v3
    [Chauffage.kicad_sch, HC05.kicad_sch, LED_internes.kicad_sch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]
2025-03-20 PCBs v4
    [Chauffage.kicad_sch, HC05.kicad_sch, LED_internes.kicad_sch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]
2025-03-20 PCBs V5
    [PCB_Aquarium2.kicad_pcb]
2025-03-22 ajoutpremiers fichiers python et maj JST XH pour la PI4
    [PCB_Aquarium2-B_Cu.gbr, PCB_Aquarium2-B_Mask.gbr, PCB_Aquarium2-B_Paste.gbr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]
2025-03-22 ajout des BOM
    [BOM.csv, BOM_CSV.csv, PCB_Aquarium2.kicad_pcb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]

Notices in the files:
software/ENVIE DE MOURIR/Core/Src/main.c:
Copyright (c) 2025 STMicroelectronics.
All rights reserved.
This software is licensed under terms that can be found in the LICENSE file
